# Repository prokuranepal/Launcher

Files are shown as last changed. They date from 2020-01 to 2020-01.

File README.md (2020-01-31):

# **Launcher**

Light-Weight Fixed Wing Drone can be launched easily by using our bare hands. But when it comes to Heavy-Weight , High Capacity Fixed Wing Drone, it cannot be launched using our bare hand. A separate device or machinery is required to launch a drone which we call a launcher.

The launcher we have designed is shown in figure. As our first objective, the launcher has been designed very modular and the design could be adjusted for both manual and automatic launching. For manual launching, one end of bungee chord is attached with slider, the bungee chord gets support from pulley and then the other end of bungee chord is attached with base. Then the slider is pulled downward using a manual winch. When the slider is down, the slider is locked using a simple lever system. After the slider is locked, the manual winch is disengaged. During this condition, the bungee chord is in high tension. The drone is attached on the slider. A system to attach drone with slider is yet to be designed. The concept has already been developed, the only thing remaining is accurate dimensions or measurements which completely depends on size of drone.

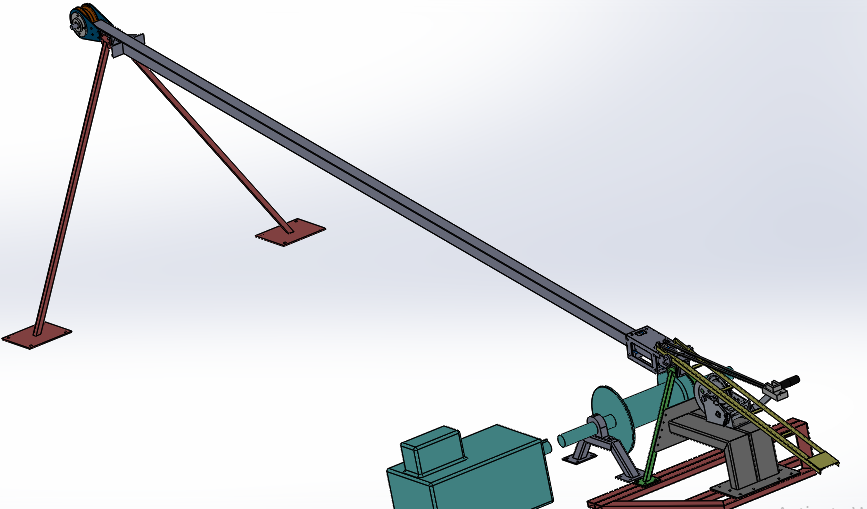
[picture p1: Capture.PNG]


Now to release a slider, we have to press the longer end of lever through our feet. For automatic launching, one end of rope is attached with slider, a rope gets support from pulley and other end of rope is attached with winch. That winch is coupled with high speed & high torque motor through coupler and / or clutch. For our recent purpose, we are only focusing on manual launching using bungee chord. The motor and winch could be added on design later on modularly.

One can also view 3D design of our launcher from Solidworks design file that we have attached or uploaded along. For a detail drawing, one should open a PDF file named **"Launcher Drawing1"**. To view a complete design file of launcher, one should open **"launcher"** with a file type "SOLIDWORKS Assembly Document" (.SLDASM). Other designs are only a part design for that assembly. 

Note:- A design file couldn't be opened if Solidworks has not been installed in device. Assembly file couldn't be opened if its part designs are not with it.

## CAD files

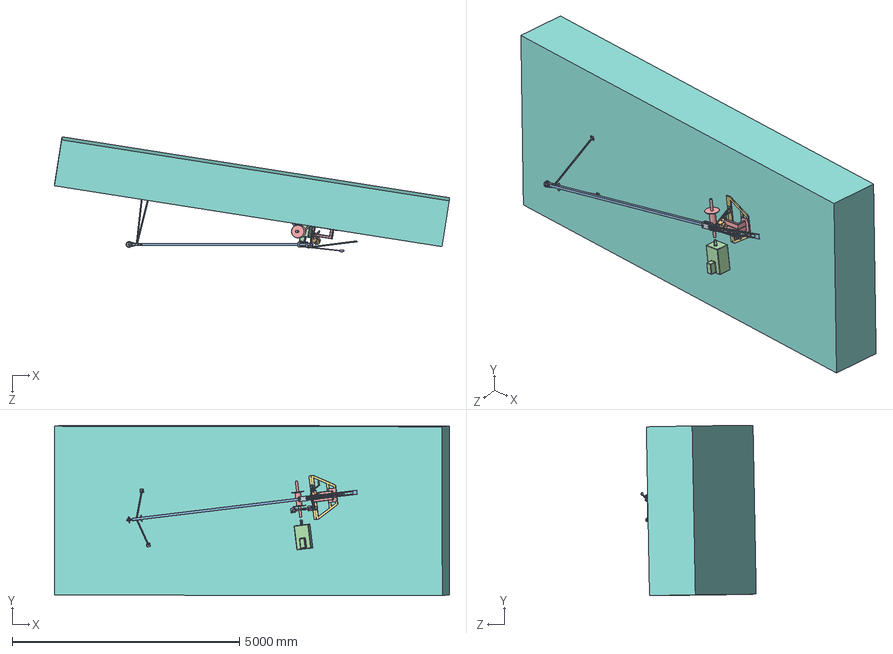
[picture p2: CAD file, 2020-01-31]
Assembly parts for drafting/SliderWithShaft.SLDASM
8683.5 x 3743.1 x 2538.9 mm
roller_1 x 8

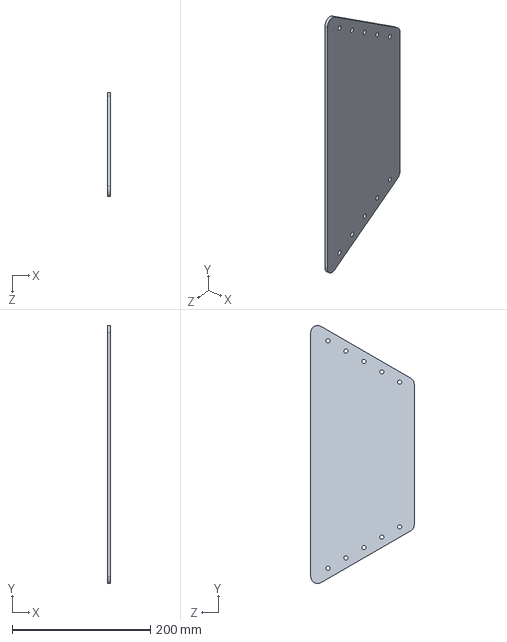
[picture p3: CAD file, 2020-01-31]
Plates/WSP1.SLDPRT
4.00 x 373.8 x 150.0 mm

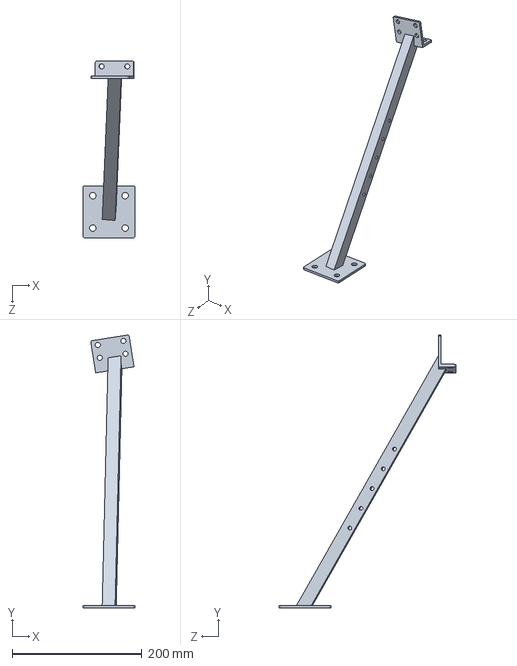
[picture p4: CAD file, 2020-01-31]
Assembly parts for drafting/Stand1ForDrafting.SLDPRT
80.0 x 421.3 x 272.6 mm

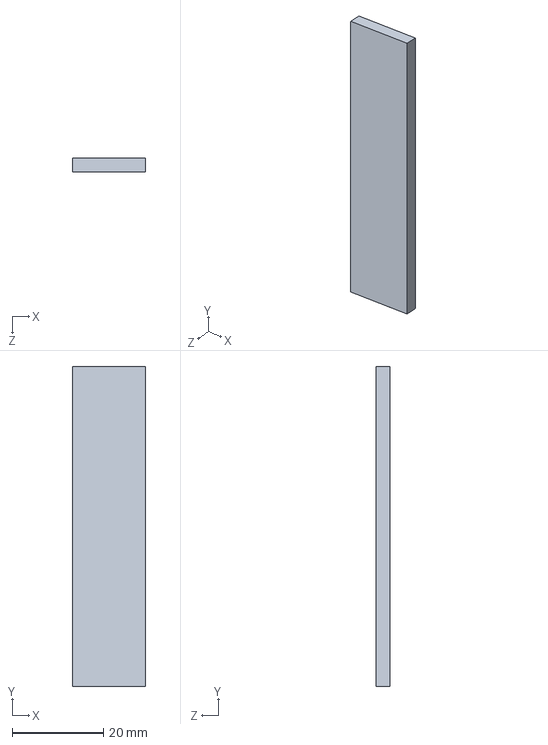
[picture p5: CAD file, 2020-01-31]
Plates/BBP1.SLDPRT
16.0 x 70.0 x 3.00 mm

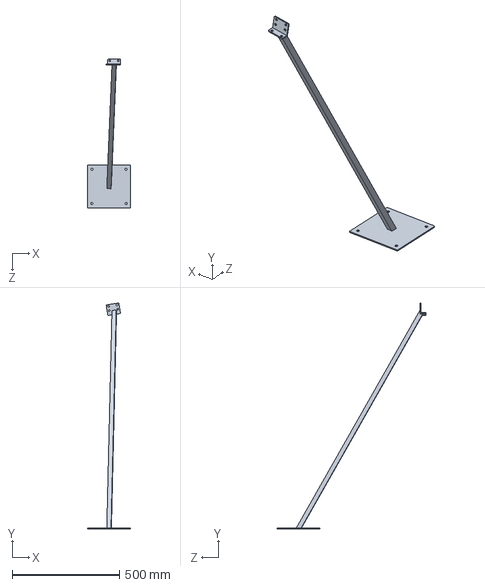
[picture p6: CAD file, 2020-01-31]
Assembly parts for drafting/Stand1.1ForDrafting.SLDPRT
200.0 x 1052.8 x 693.4 mm

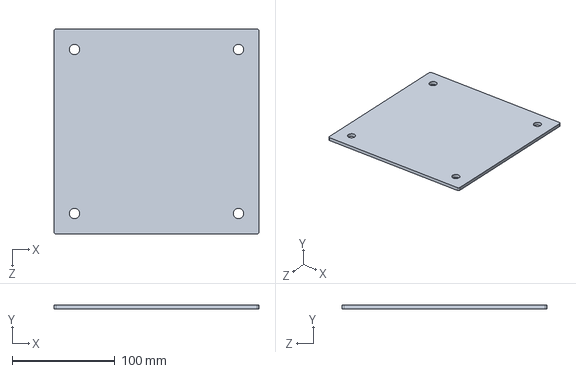
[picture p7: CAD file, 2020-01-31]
Plates/SBP2.SLDPRT
200.0 x 4.00 x 200.0 mm

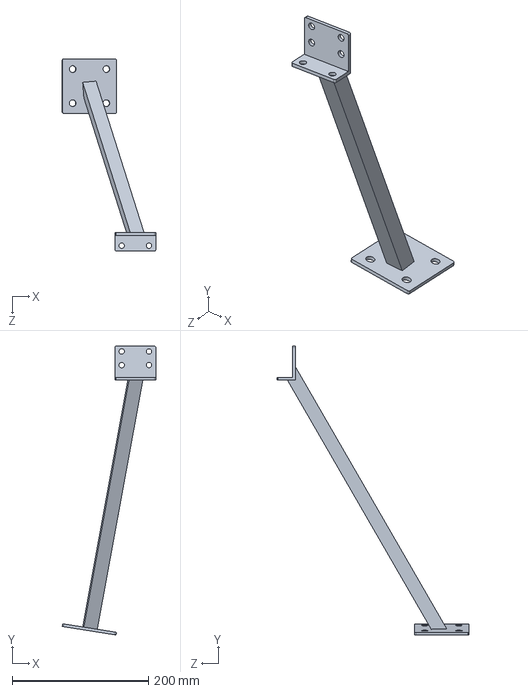
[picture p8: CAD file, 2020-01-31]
stand2.SLDPRT
137.2 x 423.6 x 281.9 mm

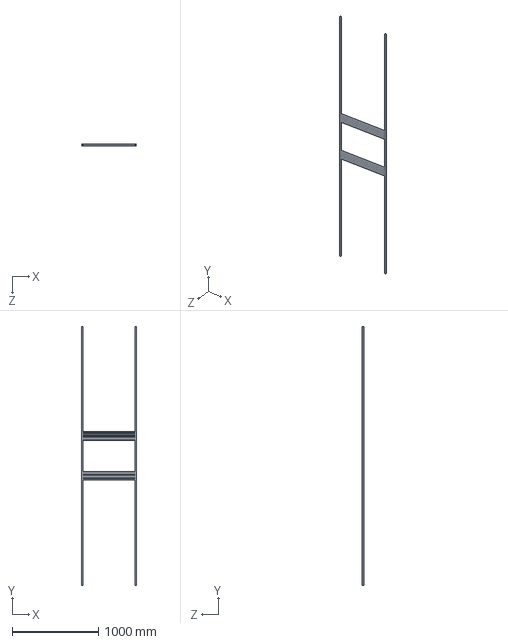
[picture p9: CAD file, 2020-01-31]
base1.SLDPRT
640.0 x 3000.0 x 20.0 mm

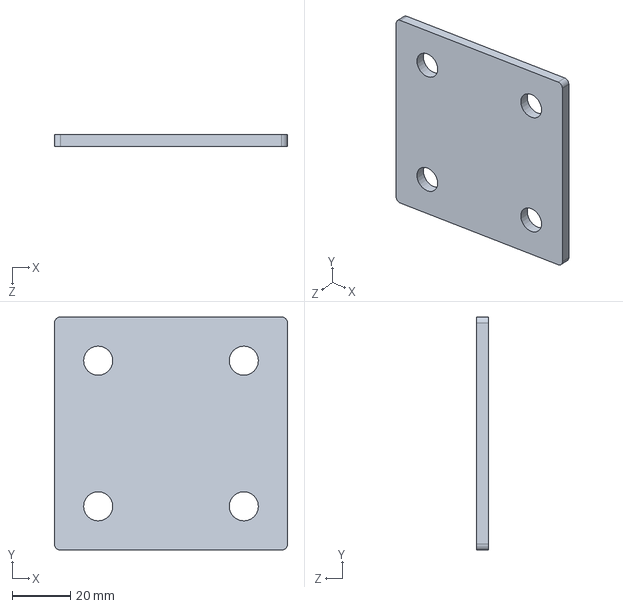
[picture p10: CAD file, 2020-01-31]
Plates/SBP1.SLDPRT
80.0 x 80.0 x 4.00 mm

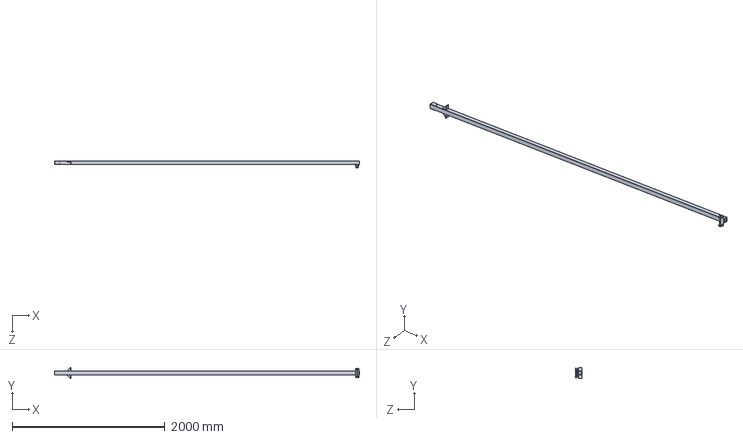
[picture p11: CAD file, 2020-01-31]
Assembly parts for drafting/ramp_1ForDrafting.SLDPRT
4000.0 x 150.8 x 95.8 mm

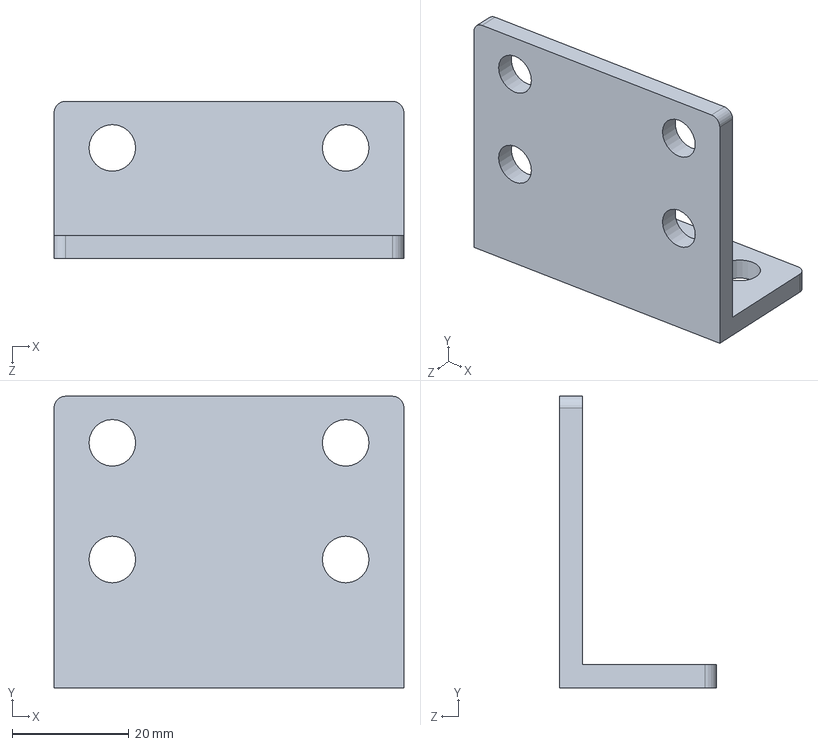
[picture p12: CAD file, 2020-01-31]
Plates/SSP1.SLDPRT
60.0 x 50.0 x 27.0 mm

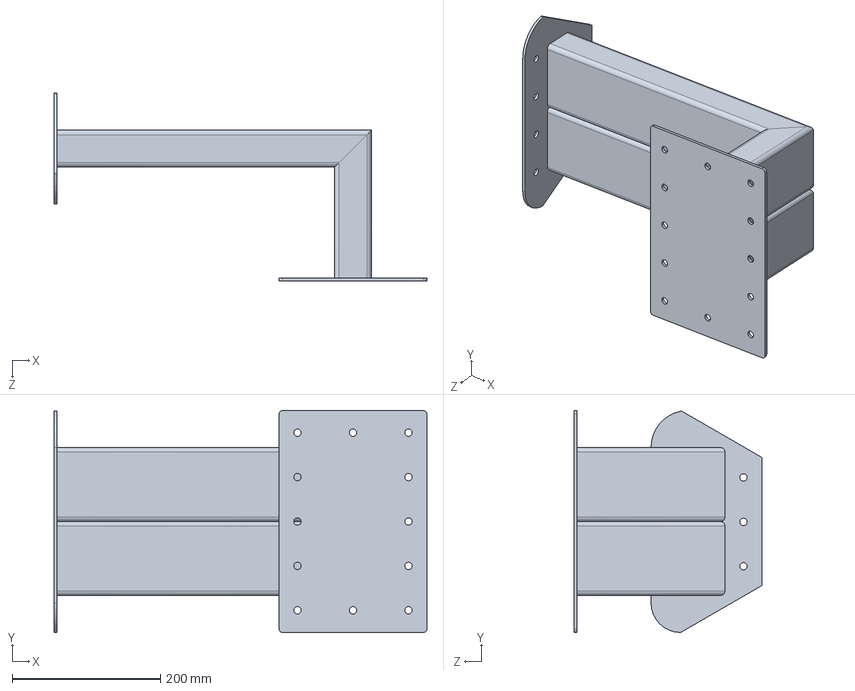
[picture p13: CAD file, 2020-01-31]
winch_base.SLDPRT
504.0 x 300.0 x 254.0 mm

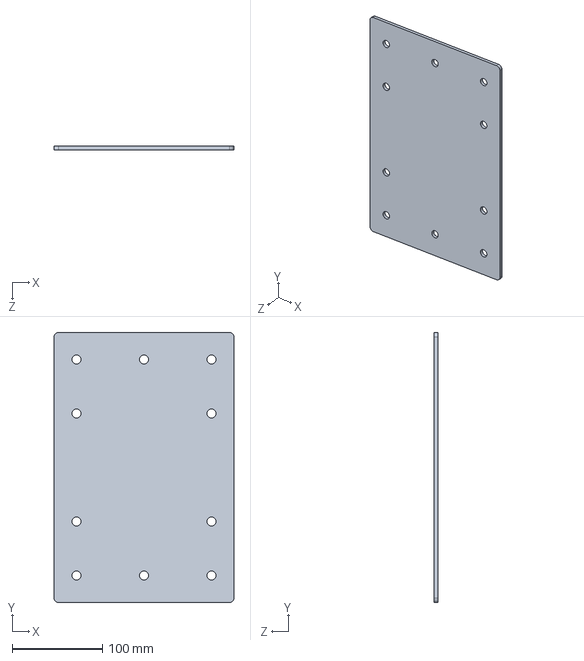
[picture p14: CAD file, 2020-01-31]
Plates/WBP1.SLDPRT
200.0 x 300.0 x 4.00 mm

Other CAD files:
Assembly parts for drafting/launcherForDrafting.SLDASM
stand2.1.SLDPRT
stand1.1.SLDPRT
Assembly parts for drafting/Stand2.1ForDrafting.SLDPRT
Assembly parts for drafting/Stand2ForDrawing.SLDPRT
Assembly parts for drafting/FulcrumForLock.SLDPRT
Base.SLDPRT
Bearing.sldprt
BearingHolder.SLDPRT
BearingHousing.SLDPRT
Bearing_base.SLDPRT
CFrod_1.sldprt
Ground.sldprt
Imported11.sldprt
Imported12.sldprt
Imported6_1.sldprt
Lock.SLDPRT
Manual_winch1.SLDPRT
Part1_1.sldprt
Part2_1.sldprt
Part3_1.sldprt
Plates/BBP2.SLDPRT
Plates/BMP.SLDPRT
Plates/LP.SLDPRT
Plates/StiffnerPlate.SLDPRT
Plates/StopPlate.SLDPRT
Plates/WBP2.SLDPRT
Pulley.sldprt
Shaft.sldprt
Support1.sldprt
Support2.SLDPRT
U-plate.sldprt
Winch.SLDPRT
Winch_support.SLDPRT
motor.SLDPRT
motor1.sldprt
motor2.sldprt
ramp_1.sldprt
roller_1.sldprt
stand1.SLDPRT

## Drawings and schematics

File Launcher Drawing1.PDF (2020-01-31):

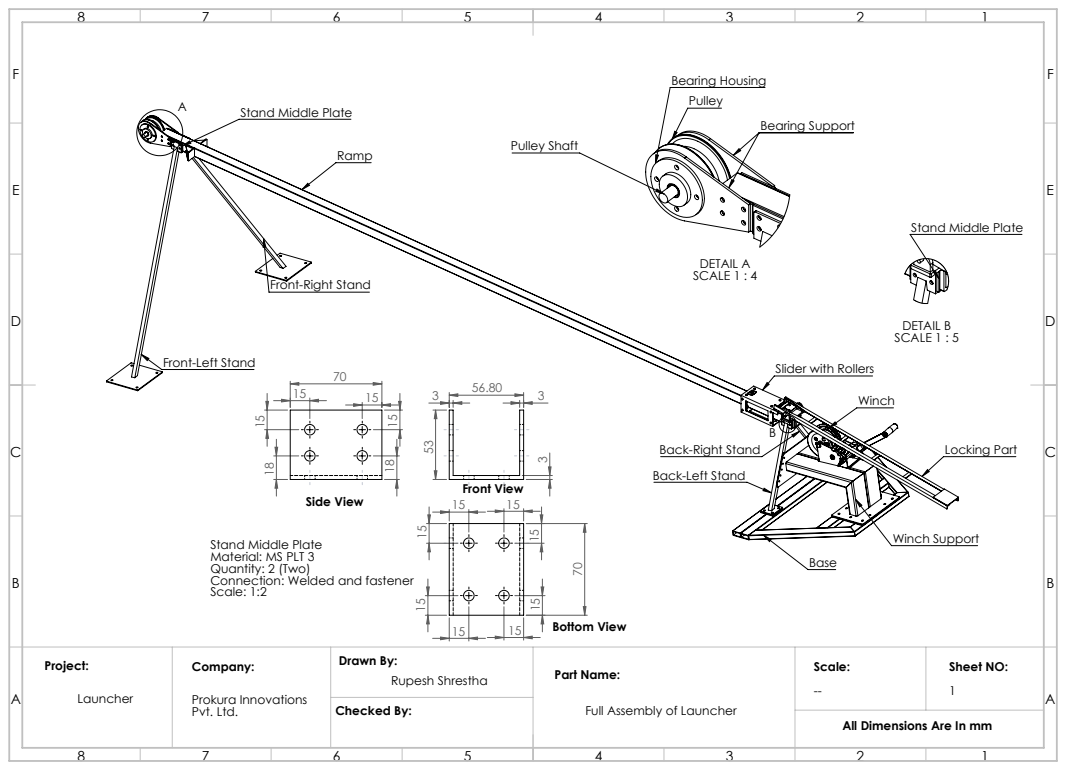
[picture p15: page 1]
Locking Part; Winch Support; Bottom View; DETAIL A SCALE 1 : 4; Bearing Support; Bearing Housing; Pulley Shaft; DETAIL B SCALE 1 : 5; Front View; Side View; Sheet NO:; Checked By:; Drawn By:; Part Name: -- Rupesh Shrestha

Stand Middle Plate

Front-Right Stand

Front-Left Stand

Slider with Rollers

Back-Right Stand
Back-Left Stand

Material: MS PLT 3
Quantity: 2 (Two)
Connection: Welded and fastener
Scale: 1:2

Full Assembly of Launcher Prokura Innovations
Pvt. Ltd.

All Dimensions Are In mm

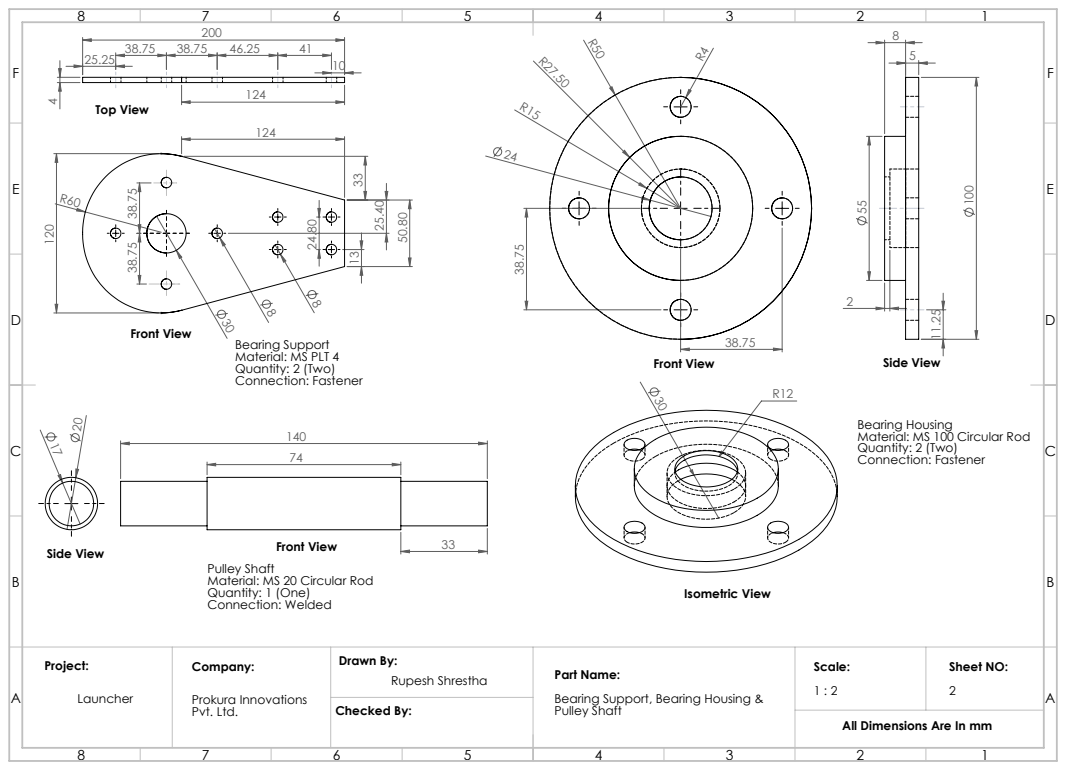
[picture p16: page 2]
Front View; Top View; Side View; Isometric View; Checked By:

Bearing Support
Material: MS PLT 4
Quantity: 2 (Two)
Connection: Fastener

Bearing Housing
Material: MS 100 Circular Rod

Pulley Shaft
Material: MS 20 Circular Rod
Quantity: 1 (One)
Connection: Welded

Project: Launcher | Company: Prokura Innovations Pvt. Ltd. | Drawn By: Rupesh Shrestha | Part Name: Bearing Support, Bearing Housing & Pulley Shaft | Scale: 1 : 2 | Sheet NO: 2

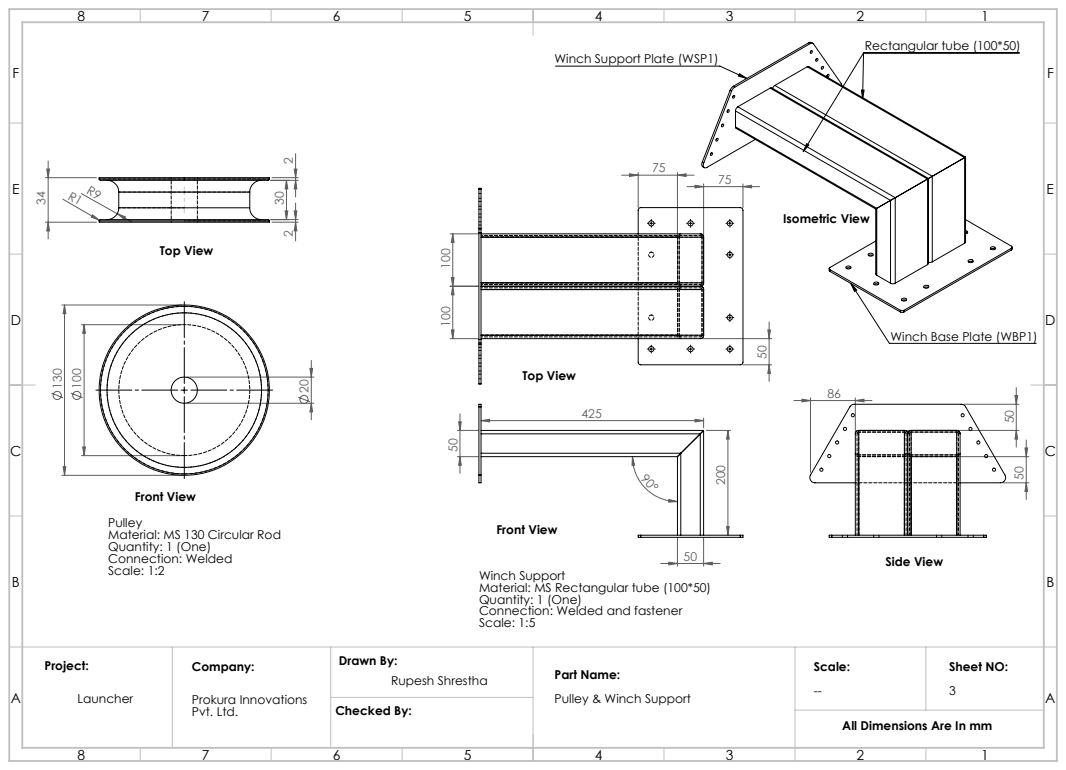
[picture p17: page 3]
Top View; Front View; Rectangular tube (100*50); Isometric View; Side View; Checked By:

Winch Support Plate (WSP1)

Winch Base Plate (WBP1) 50 50

Front View
Pulley
Material: MS 130 Circular Rod
Quantity: 1 (One)
Connection: Welded
Scale: 1:2

Winch Support
Material: MS Rectangular tube (100*50)
Connection: Welded and fastener
Scale: 1:5

Project: Launcher | Company: Prokura Innovations Pvt. Ltd. | Drawn By: | Part Name: Pulley & Winch Support | Scale: -- Rupesh Shrestha | Sheet NO: 3

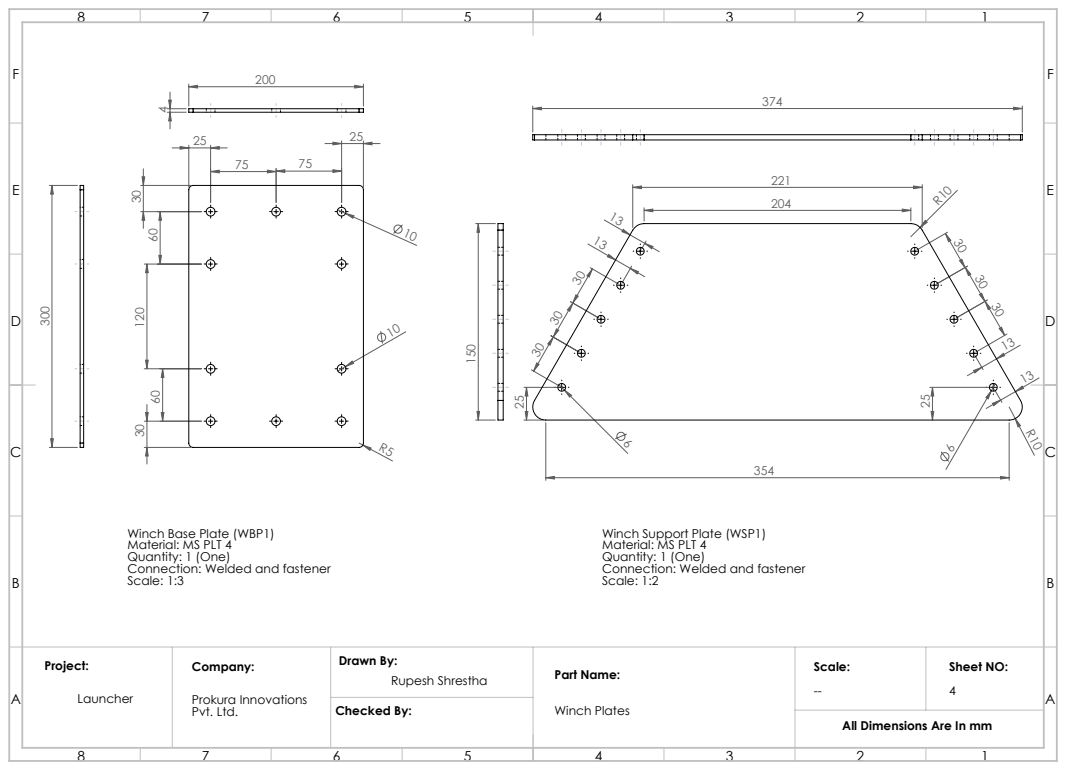
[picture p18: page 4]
Checked By:

Winch Base Plate (WBP1)
Material: MS PLT 4
Quantity: 1 (One)
Connection: Welded and fastener
Scale: 1:3

Winch Support Plate (WSP1)
Scale: 1:2

Project: Launcher | Company: Pvt. Ltd. | Drawn By: | Part Name: | Scale: -- Rupesh Shrestha | Sheet NO: 4

Winch Plates Prokura Innovations

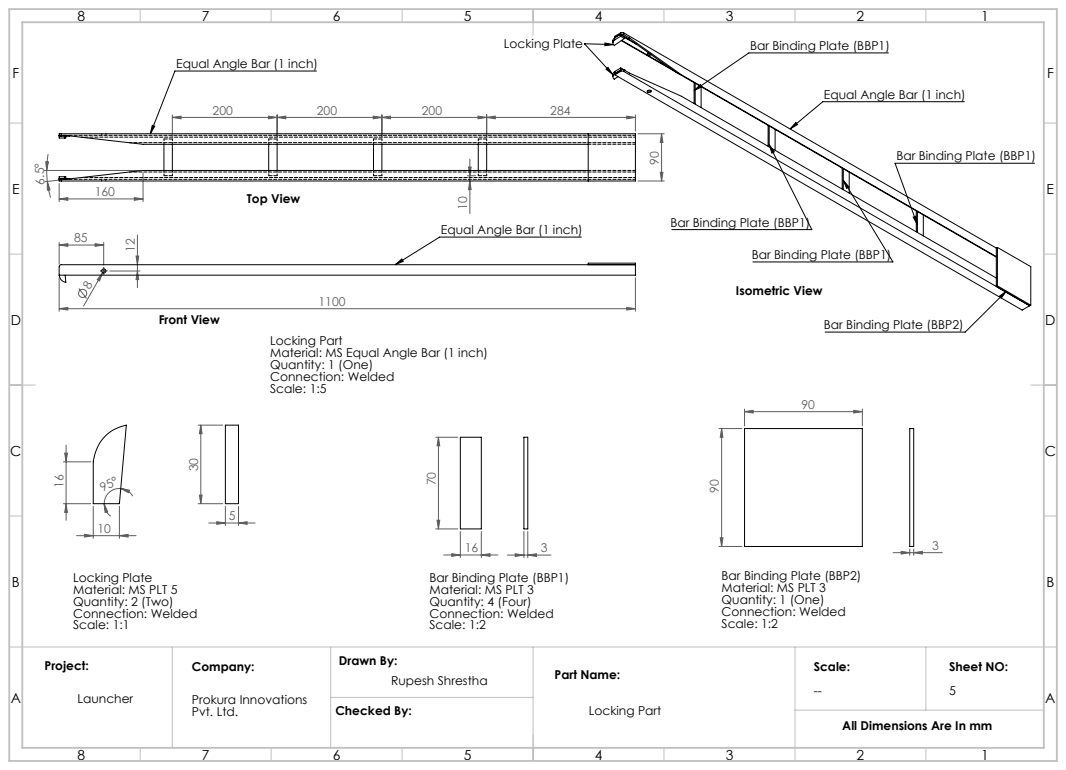
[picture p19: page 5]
Top View; Locking Plate; Isometric View; Front View; Checked By:

Bar Binding Plate (BBP1)

Equal Angle Bar (1 inch)

Bar Binding Plate (BBP2)

Locking Part
Material: MS Equal Angle Bar (1 inch)
Quantity: 1 (One)
Connection: Welded
Scale: 1:5

Material: MS PLT 3
Quantity: 4 (Four)
Scale: 1:2

Locking Plate
Material: MS PLT 5
Quantity: 2 (Two)
Scale: 1:1

Project: Launcher | Company: Pvt. Ltd. | Drawn By: | Part Name: | Scale: -- Rupesh Shrestha | Sheet NO: 5

Locking Part Prokura Innovations

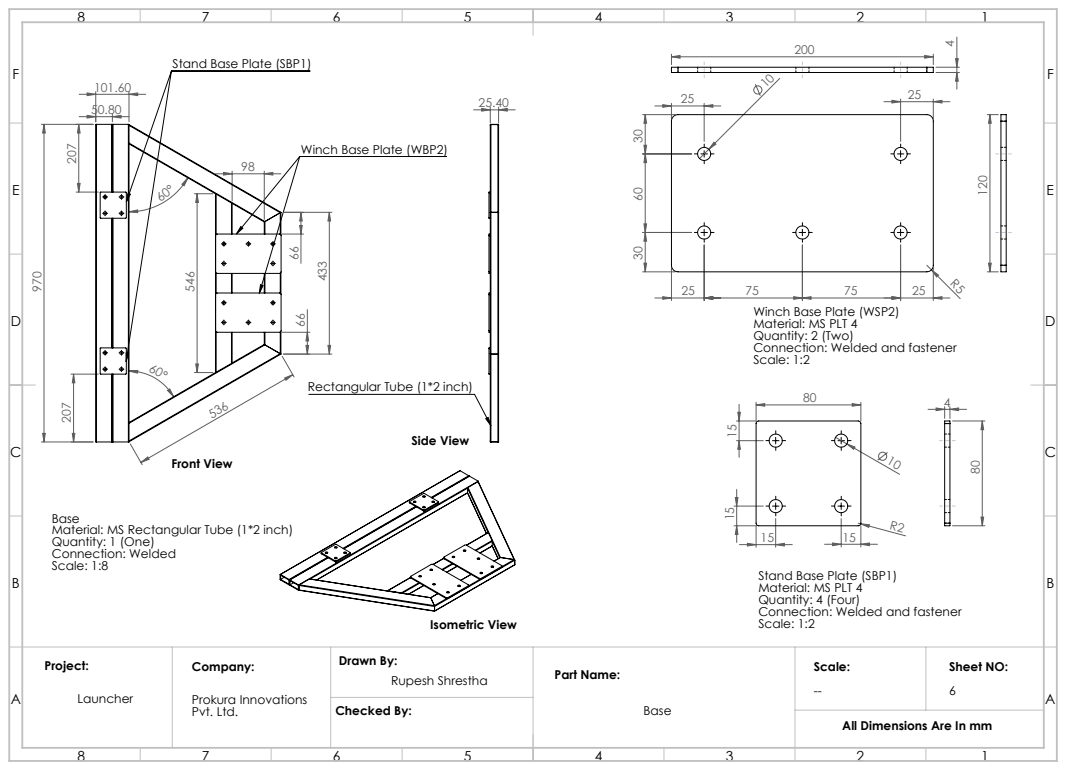
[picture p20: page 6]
Front View; Side View; Isometric View; Checked By:

Stand Base Plate (SBP1)

Winch Base Plate (WBP2)

Winch Base Plate (WSP2)
Material: MS PLT 4
Quantity: 2 (Two)
Connection: Welded and fastener
Scale: 1:2

Rectangular Tube (1*2 inch)

Base
Material: MS Rectangular Tube (1*2 inch)
Quantity: 1 (One)
Connection: Welded
Scale: 1:8

Quantity: 4 (Four)

Project: Launcher | Company: Pvt. Ltd. | Drawn By: | Part Name: | Scale: -- Rupesh Shrestha | Sheet NO: 6

Base Prokura Innovations

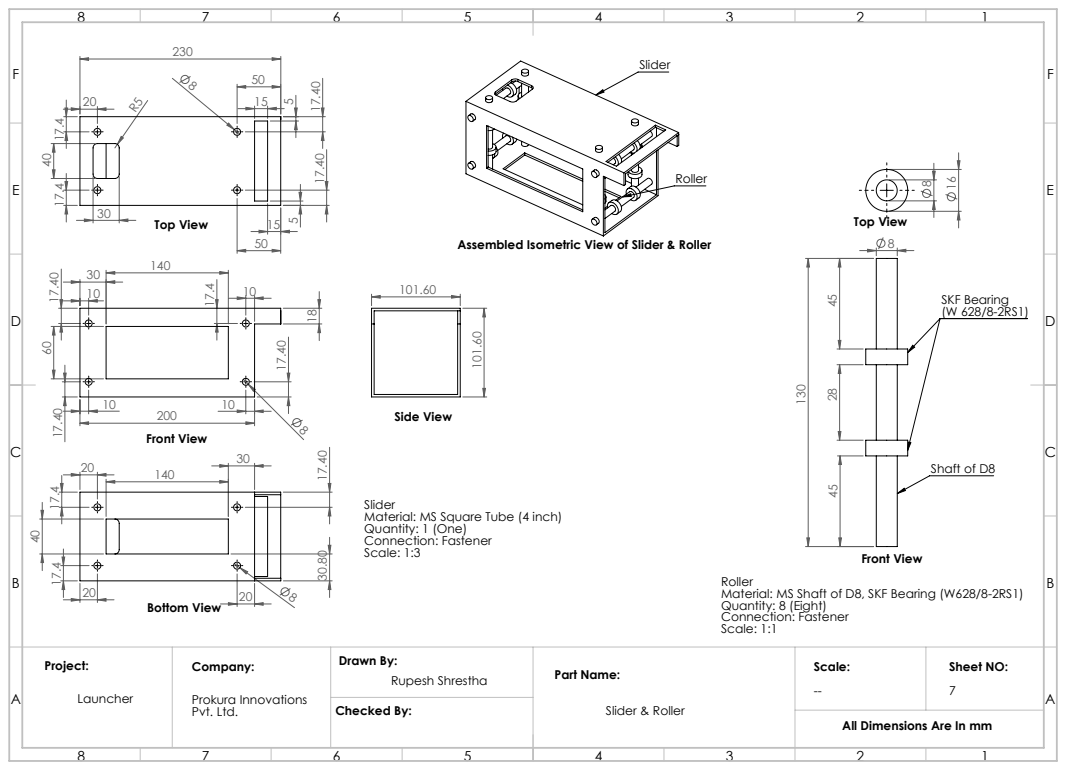
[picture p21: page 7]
Top View; Bottom View; Side View; SKF Bearing (W 628/8-2RS1); Shaft of D8; Front View; Sheet NO:; Checked By:; Drawn By:; Part Name: -- Rupesh Shrestha

Assembled Isometric View of Slider & Roller

Slider
Material: MS Square Tube (4 inch)
Quantity: 1 (One)
Connection: Fastener
Scale: 1:3

Roller
Material: MS Shaft of D8, SKF Bearing (W628/8-2RS1)
Quantity: 8 (Eight)
Scale: 1:1

Slider & Roller Prokura Innovations
Pvt. Ltd.

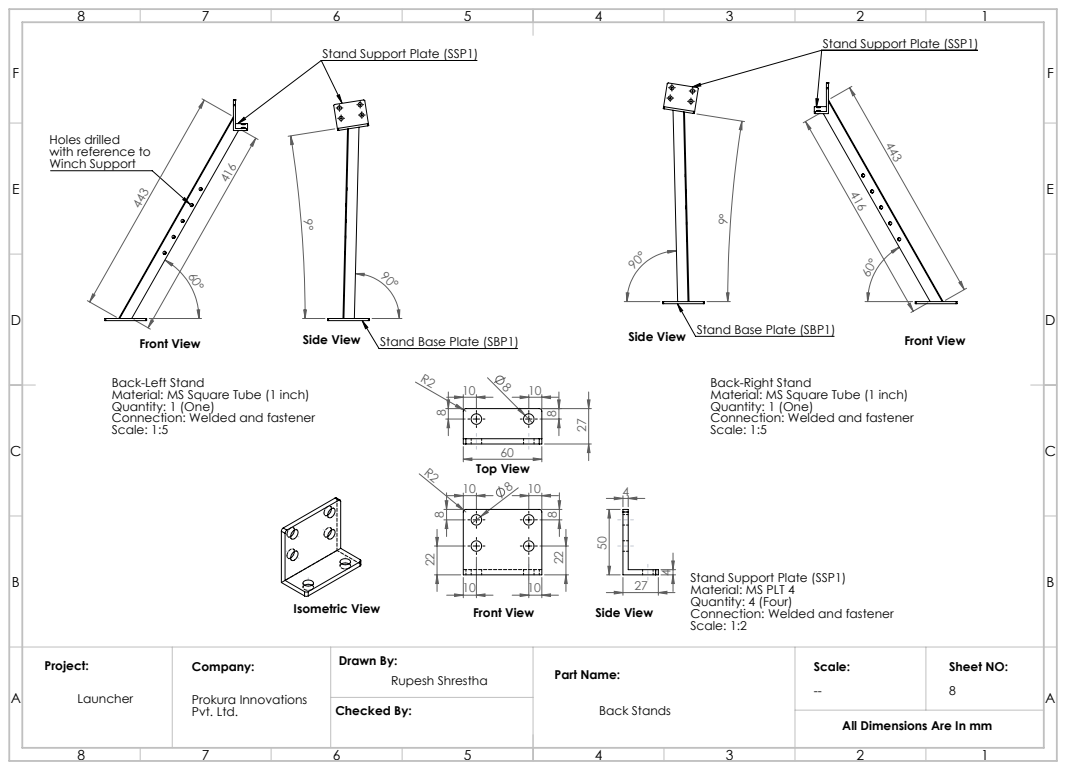
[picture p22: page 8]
Front View; Top View; Isometric View; Side View; Sheet NO:; Checked By:; Drawn By:; Part Name: -- Rupesh Shrestha

Stand Support Plate (SSP1)

Holes drilled
with reference to
Winch Support

Stand Base Plate (SBP1)

Back-Left Stand
Material: MS Square Tube (1 inch)
Quantity: 1 (One)
Connection: Welded and fastener
Scale: 1:5

Back-Right Stand

Material: MS PLT 4
Quantity: 4 (Four)
Scale: 1:2

Back Stands Prokura Innovations
Pvt. Ltd.

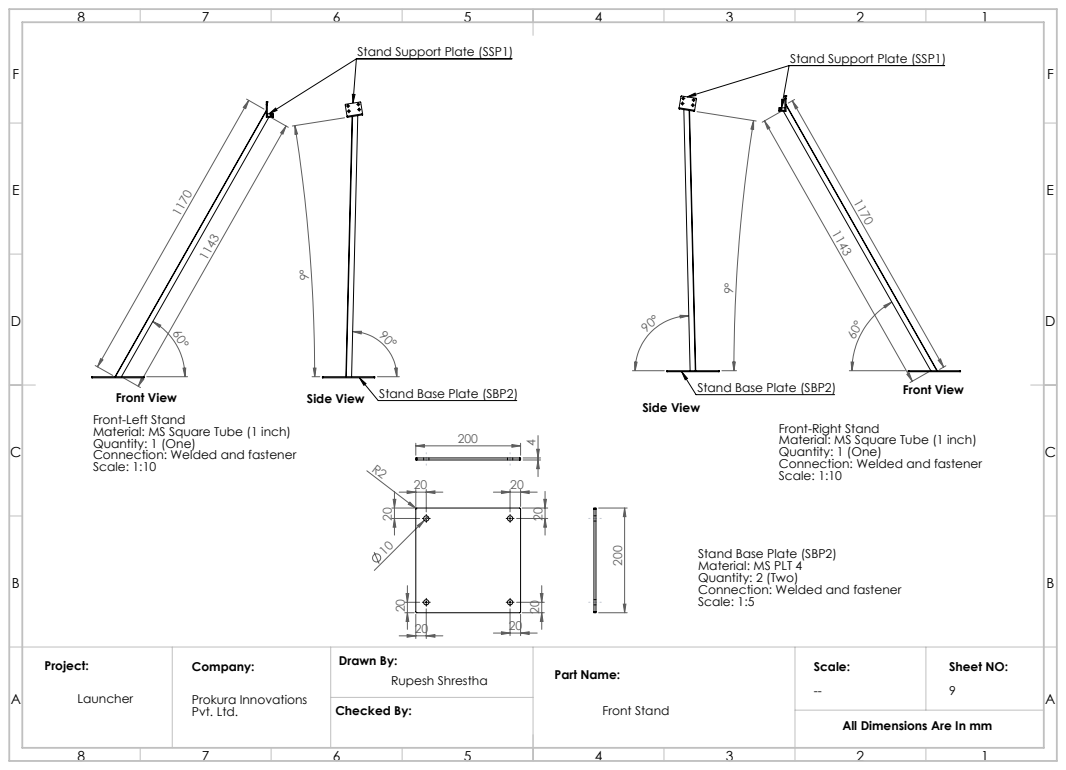
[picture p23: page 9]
Front View; Side View; Sheet NO:; Checked By:; Drawn By:; Part Name: -- Rupesh Shrestha

Stand Support Plate (SSP1)

Stand Base Plate (SBP2)

Front View
Front-Left Stand
Material: MS Square Tube (1 inch)
Quantity: 1 (One)
Connection: Welded and fastener
Scale: 1:10

Stand Base Plate (SBP2) Side View

Front-Right Stand

Material: MS PLT 4
Quantity: 2 (Two)
Scale: 1:5

Front Stand Prokura Innovations
Pvt. Ltd.

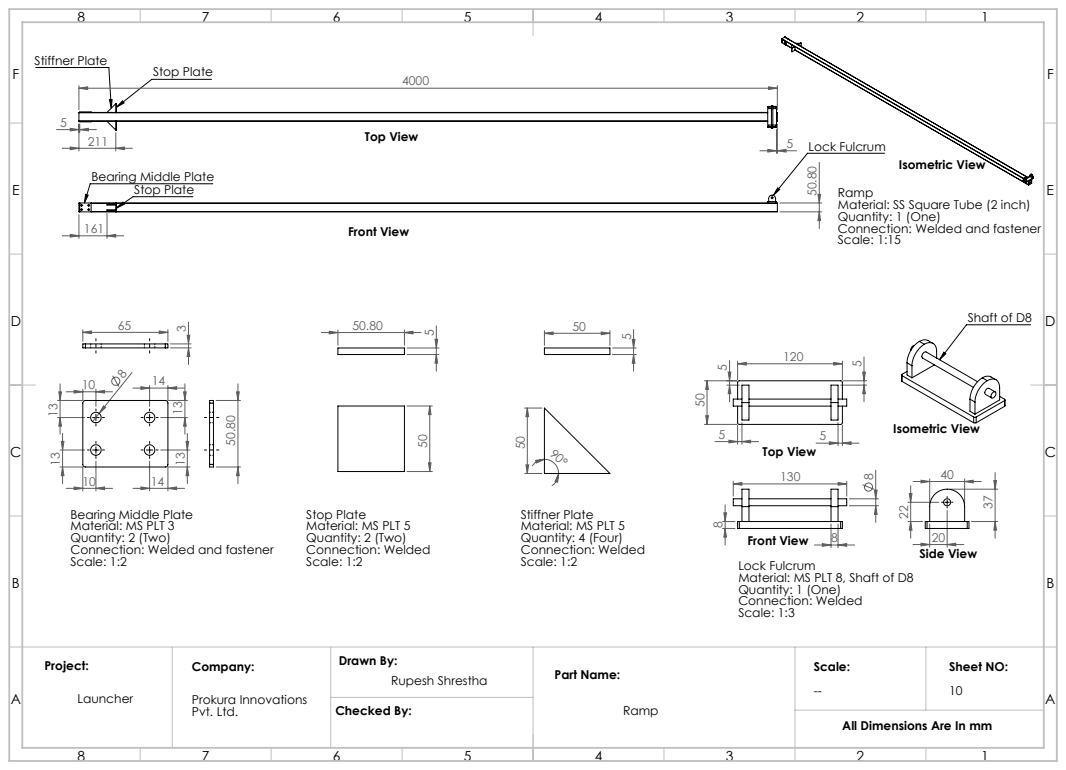
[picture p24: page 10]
Lock Fulcrum; Front View; Stop Plate; Stiffner Plate; Top View; Isometric View; Shaft of D8; Scale: 1:2; Side View; Checked By:

Bearing Middle Plate
Stop Plate

Ramp
Material: SS Square Tube (2 inch)
Quantity: 1 (One)
Connection: Welded and fastener
Scale: 1:15
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

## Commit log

2020-01-28 1st stage complete
    [Base.SLDPRT, Bearing.sldprt, BearingHolder.SLDPRT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]
2020-01-31 Add readme file. Add Launcher Drawing.pdf.
    [BBP1.SLDPRT, BBP2.SLDPRT, BMP.SLDPRT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]
